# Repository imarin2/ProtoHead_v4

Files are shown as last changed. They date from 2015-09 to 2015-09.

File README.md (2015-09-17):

# ProtoHead_v4

This repository includes all the design and manufacturing information for a Protohead v4 DIY FABtotum head. This head is not fully tested yet. Do not expect just to 3d print the parts, mill the PCB, put everything together and outperform the stock head. It is just a first effort towards having a reference design that just "works" (within the limitations that will sure arise), so that others can get started and improve the design.

Note: There is an alternative PCB featuring 24 V and servo1 connections in here:
https://github.com/imarin2/Protohead_PCB_v4_FAB_24V

# So what is this in short?

A Bowden type hotend print only FABtotum head looking like this:

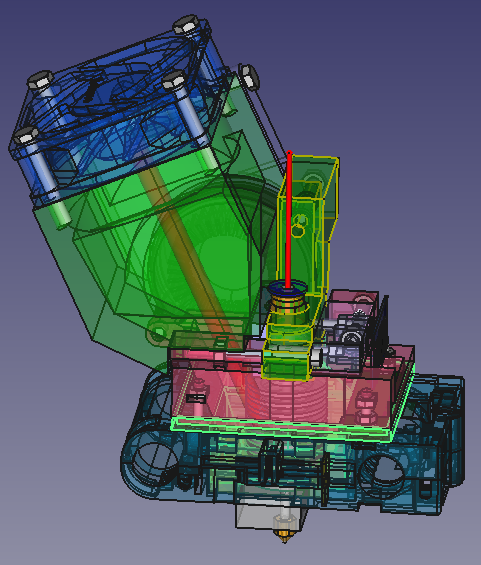
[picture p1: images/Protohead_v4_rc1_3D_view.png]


It is based on a low cost almost all metal hotend with reference 3DA-002 (long version, so coming with a press-fit) and looking something like this:
https://grabcad.com/library/hotend-3da-002-1

The "mechanical design" is made in FreeCAD and the full source is included.

The PCB is designed in KiCAD. It uses this KiCAD library for the bourn connector:
https://github.com/imarin2/FABHeadLibraries

The library has schematic and footprint for the FABtotum head bourns connector:

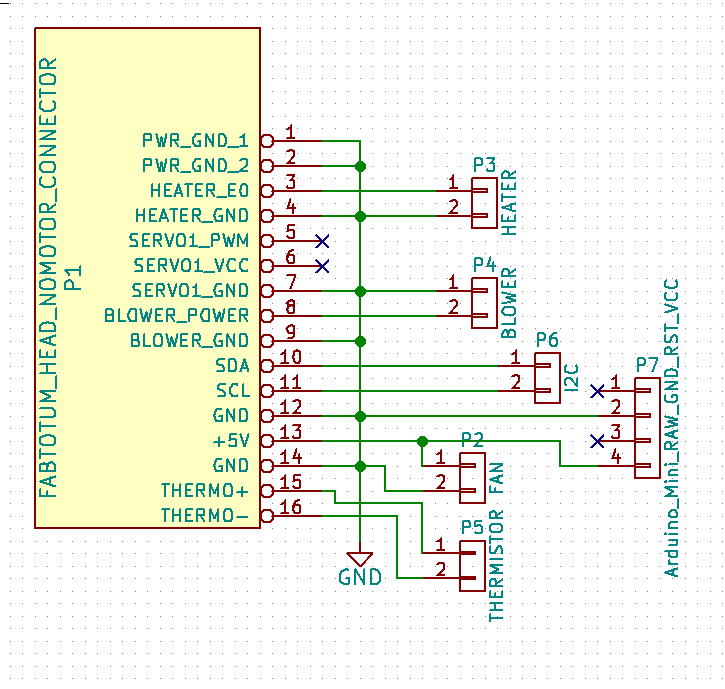
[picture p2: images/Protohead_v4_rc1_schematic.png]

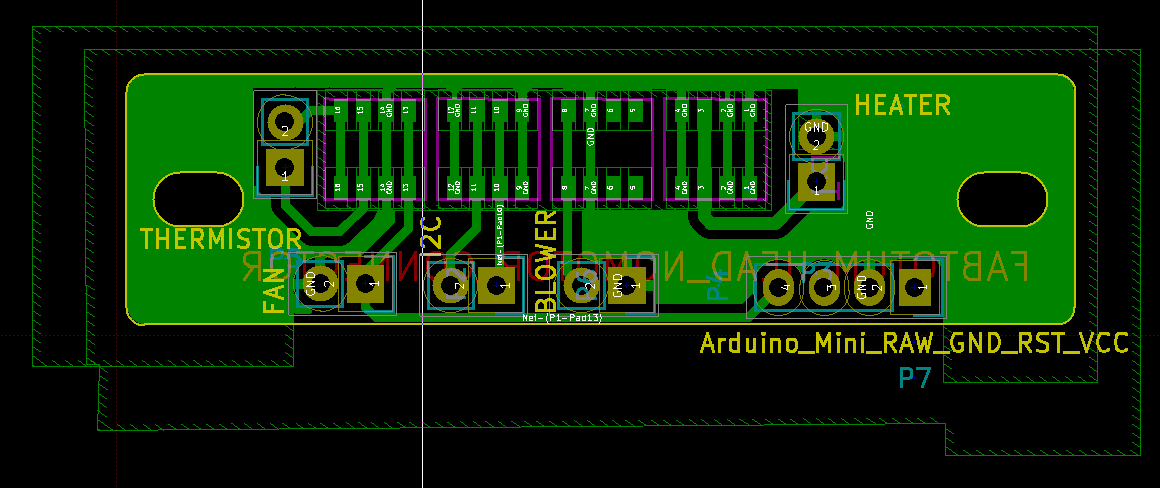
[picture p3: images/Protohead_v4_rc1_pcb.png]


The PCB is quite small and looks like this:
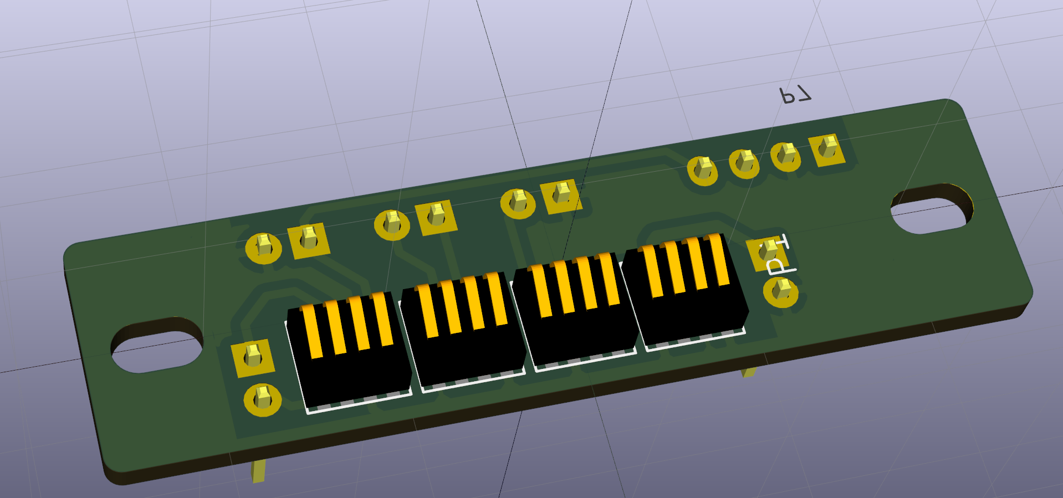
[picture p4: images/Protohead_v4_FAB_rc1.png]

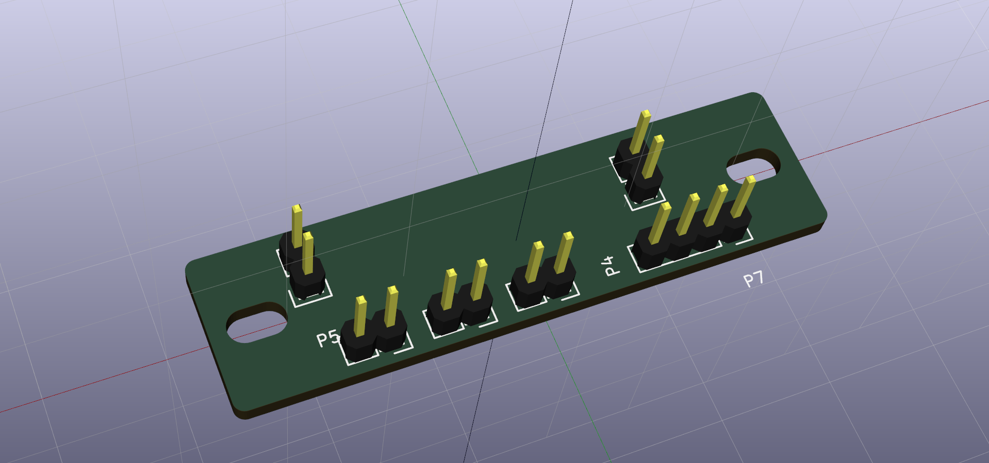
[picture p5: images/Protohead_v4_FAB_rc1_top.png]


It also includes the Gerbers, DXF, Heekscad project (cutout) and FlatCAM project (milling the PCB), as well as the Marlin flavoured gcode (post-processed as described in the Fabtotum wiki) for manufacturing it.

The PCB has to slot shapes to be attached to the printed parts using M3 screws and nuts, the slots allowing some play as to move the PCB and fasten it when correctly aligned with the Carriage.

The design requires of an Arduino Mini Pro to be available separately and attach to the PCB via a 4 pin angled header. The I2C pins must be connected separately using a cable. The firmware for the Arduino (currently only identifying itself as 0xFFFFFFFF) is here:
https://github.com/imarin2/ProtoHead

# Is this tested?
- I tested it without having mounted the Axial fan. It worked half a calibration cube (I2C identification obviously worked), then it clogged because the heatsink of the cold-end had no cooling.
- It misses one stil-to-be-designed part to be attached to the blower output to redirect air to the nozzle for cooling the part.
- I am currently waiting for the axial fan and a blower with the current voltage to arrive.

# What do I need to make it?
- An arduino mini pro, I have the one with the 368 chip, but any would do.
- A 3DA-002 (long version, so coming with a press-fit) with a 24V heater (sometimes is cheaper to get one with a 12V cartrige and buy a 24V cartridge separately). The thermistor that comes with them is generally a type 11 that, I hope, will be supported soon in FABlin if my last pull-request is merged.
- A 5V blower fan 5015S DC 5V 50x50x15mm
- An axial fan 60x60 mm, 5V.
- M4 and M3 bolts and nuts of different sizes (I will hopefully make a list some day, see the FreeCAD source).

# Why share it?

Well, I am not aware of another "full DIY kit". Somebody may actually save some time by starting here. It may serve as a reference design to accelerate to arrive to a starting working step to those of you that can surely improve it.

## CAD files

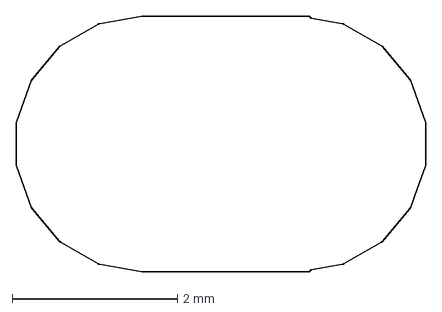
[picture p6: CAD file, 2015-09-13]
manufacturing/cutout/Protohead_v4_FAB_rc1-Edge_Cuts_librecad_right_inner.dxf
4.95 x 3.10 mm

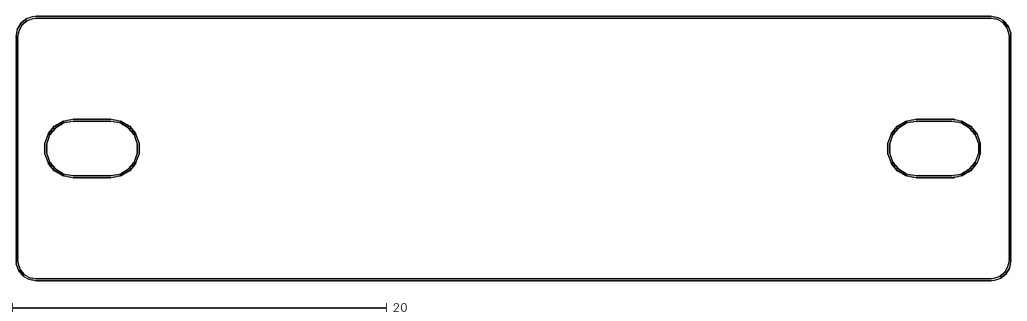
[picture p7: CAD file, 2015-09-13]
manufacturing/cutout/Protohead_v4_FAB_rc1-Edge_Cuts.dxf
53.1 x 14.1

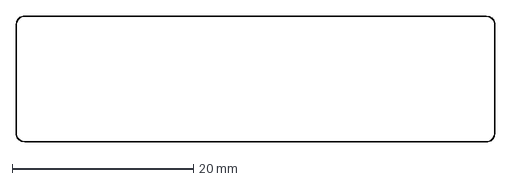
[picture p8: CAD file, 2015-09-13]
manufacturing/cutout/Protohead_v4_FAB_rc1-Edge_Cuts_librecad_outer.dxf
52.9 x 13.9 mm

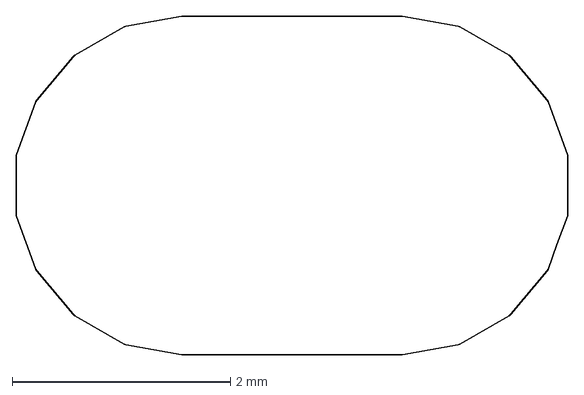
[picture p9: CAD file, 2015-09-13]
manufacturing/cutout/Protohead_v4_FAB_rc1-Edge_Cuts_librecad_left_inner.dxf
5.05 x 3.10 mm

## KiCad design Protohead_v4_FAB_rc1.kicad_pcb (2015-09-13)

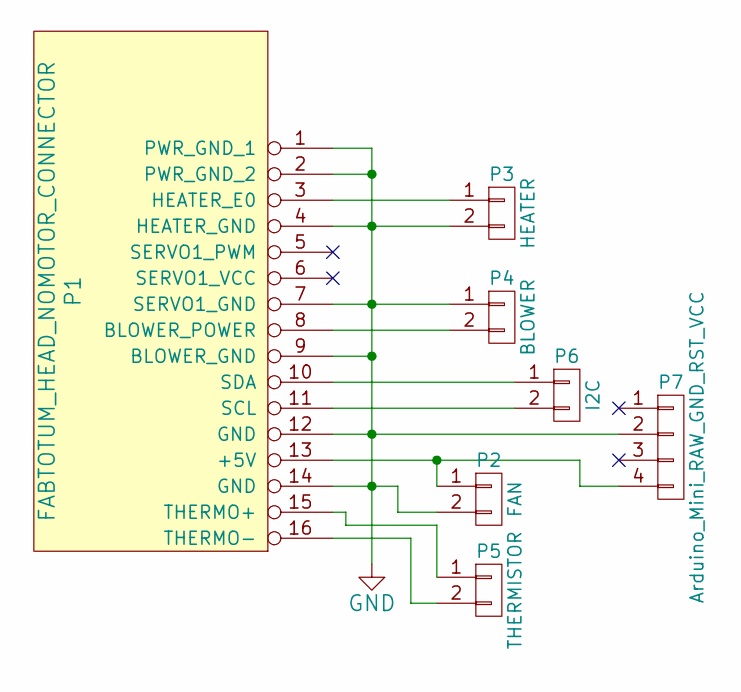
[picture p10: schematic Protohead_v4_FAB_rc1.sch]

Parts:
P1: FABTOTUM_HEAD_NOMOTOR_CONNECTOR; IntegratedBourns_nomotor_smd
P2: FAN; Pin_Header_Straight_1x02
P3: HEATER; Pin_Header_Straight_1x02
P4: BLOWER; Pin_Header_Straight_1x02
P5: THERMISTOR; Pin_Header_Straight_1x02
P6: I2C; Pin_Header_Straight_1x02
P7: Arduino_Mini_RAW_GND_RST_VCC; Socket_Strip_Straight_1x04

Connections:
GND: P1.1 (PWR_GND_1), P1.2 (PWR_GND_2), P1.4 (HEATER_GND), P1.7 (SERVO1_GND), P1.9 (BLOWER_GND), P1.12 (GND), P1.14 (GND), P2.2, P3.2, P4.1, P7.2
unnamed: P1.3 (HEATER_E0), P3.1
unnamed: P1.8 (BLOWER_POWER), P4.2
unnamed: P1.10 (SDA), P6.1
unnamed: P1.11 (SCL), P6.2
unnamed: P1.13 (+5V), P2.1, P7.4
unnamed: P1.15 (THERMO+), P5.1
unnamed: P1.16 (THERMO-), P5.2

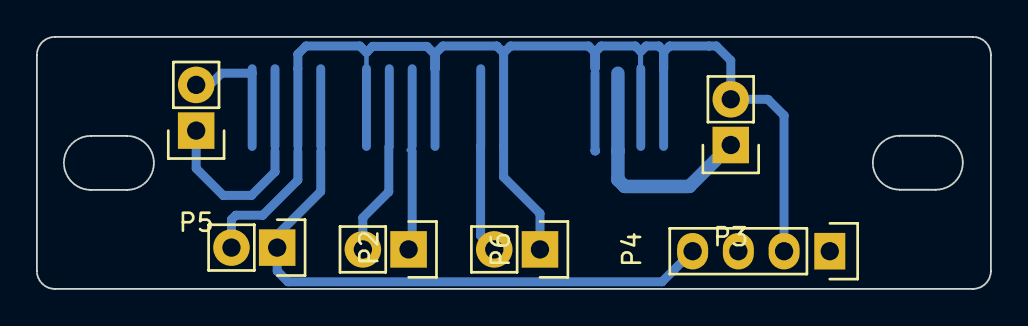
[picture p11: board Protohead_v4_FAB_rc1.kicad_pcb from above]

Board: 2 copper layers, 53.0 x 14.0 mm, 7 parts (1 on the bottom side), 8 nets.

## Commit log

2015-09-13 DIY head PCB KiCAD
    [Protohead_v4_FAB_rc1.kicad_pcb, Protohead_v4_FAB_rc1.sch]
2015-09-13 Heekscad PCB edge cutout
2015-09-13 Cutout DXF files
    KiCAD DXF output
    KiCAD DXF output post-processed in separate loops with librecad
    [Protohead_v4_FAB_rc1-Edge_Cuts.dxf, Protohead_v4_FAB_rc1-Edge_Cuts_librecad_left_inner.dxf, Protohead_v4_FAB_rc1-Edge_Cuts_librecad_outer.dxf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]
2015-09-13 KiCAD gerber output
    [Protohead_v4_FAB_rc1-B_Cu.gbr, Protohead_v4_FAB_rc1-Edge_Cuts.gbr, Protohead_v4_FAB_rc1-F_Cu.gbr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]
2015-09-13 Flatcam project and processed (via processing sh script to adapt output for Marlin) gcode output
2015-09-17 Update to link 24V version
